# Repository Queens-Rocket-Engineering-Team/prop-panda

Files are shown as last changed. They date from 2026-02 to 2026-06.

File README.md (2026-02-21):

# PANDA Control Board

PANDA (Propulsion Actuation and Nominal Data Acquisition) is the control PCB for the Queen's Rocket Engineering Team's
hybrid rocket engine. During launch, PANDA controls systems on the fill plumbing panel, controls rocket ignition, and
provides pre-launch data acquisition. PANDA also functions as a standalone static fire test stand controller that
can execute all aspects of a hot-fire test.

## Assembled PCB

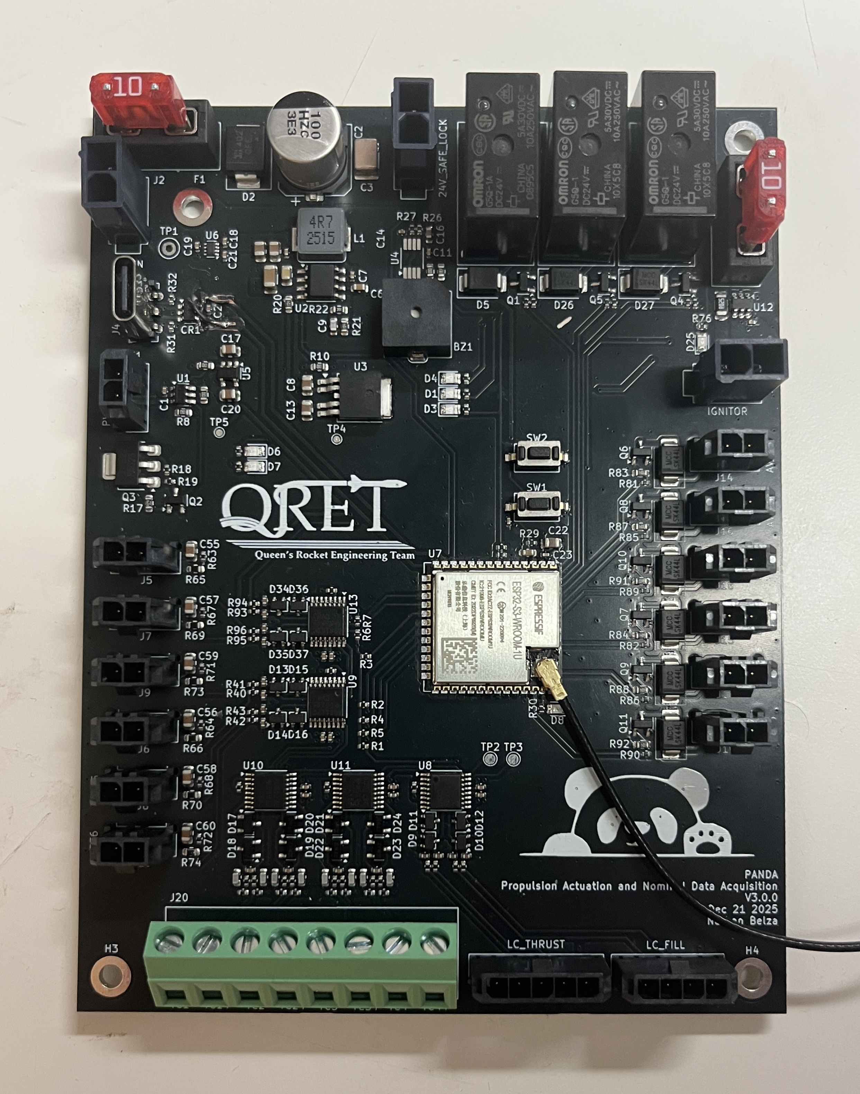
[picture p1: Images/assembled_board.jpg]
Assembled PANDA PCB


## System Architecture

PANDA uses an ESP32S3-WROOM-1U microcontroller for systems control. This ESP32S3 communicates with an external control
server to for remote control and data streaming over 2.4GHz WiFi. All commands are sent from the external server, as
PANDA does not autonomously control any systems.

Five ADS112C04 ADCs provide sensor readings to the ESP32S3 over an I2C bus. Sensors supported are:

- 6 pressure transducers
- 4 thermocouples
- 2 load cells

PANDA is also capable of monitoring ignitor characteristics. Measurements of the current passing through a nichrome wire
ignitor are obtained using a current sense amplifier across a shunt resistor in the ignitor path. Ignitor resistance
readings are also measured by injecting a small current from an IDAC on an ADC, and
measuring the resulting voltage.

A communications diagram for PANDA can be seen below.

```mermaid
---
title: PANDA Communications Flow
---
flowchart LR

    ADC(ADS112C04<br>ADCs) <==I2C==> ESP(ESP32 MCU)

    subgraph Controls
        AV(Actuated Valves)
        24VSAFE[24VSAFE<br>Relay]
        RUN[Ignitor Run<br>Relay]
        PRIME[Ignitor Prime<br>Relay]
    end

    subgraph Sensors
        PT(Pressure Transducers)
        TC(Thermocouples)
        LC(Load Cells)
        CUR(Ignitor Current)
        RES(Ignitor Resistance)
    end

    PT --> ADC
    TC --> ADC
    LC --> ADC
    CUR --> ADC
    RES --> ADC

    ESP --> AV
    ESP -->24VSAFE
    ESP --> RUN
    ESP --> PRIME

    ESP <-. WiFI .-> WIFI(External Server)
```

## Power Architecture

PANDA operates from a 24VDC power supply, and has a maximum current rating of 10A. The 24V rail is first stepped down to 5.3V with a switching converter and then dropped to 5V and 3.3V with LDOs. The 5V rail supplies analog systems, and the 3.3V rail supplies digital systems. Using LDOs on the switching output allows for low-noise power for analog measurements.

The 24VSAFE rail is only be energized when the fill panel is vacated, as it powers hazardous components such as the ignitor. The ignitor utilizes two relays in series for additional redundancy, and to ensure ignition is always intentional. A power distribution chart of PANDA can be seen below. This graph does not include the power sequencing and filtering present on the board.

```mermaid
---
title: PANDA Power Distribution
---
flowchart LR

    24VIN([24VIN]) --> 24VSAFE[24VSAFE<br>Relay]

    subgraph Valves
        AV(Valves)
        AVSAFE(Fill Valve<br>Run Valve)
    end
    24VIN --> AV
    24VSAFE --> AVSAFE

    subgraph Ignitor
        RUN[Ignitor Run<br>Relay]
        RUN --> PRIME[Ignitor Prime<br>Relay]
        PRIME --> IGN(Ignitor)
    end

    24VSAFE --> RUN[Ignitor Run<br>Relay]

    subgraph Voltage Regulation
        BUCK([5.3V Buck])
        BUCK --> 5V([5V LDO])
        BUCK --> 3V3([3.3V LDO])
    end

    24VIN --> BUCK([5.3V Buck])

    subgraph Sensors
        PT(Pressure Transducers)
        LC(Load Cells)
        RES(Ignitor Current<br>Sensor)
    end

    5V --> ADC(ADS112C04<br>ADCs)
    3V3 --> ESP(ESP32 MCU)
    3V3 --> ADC
    24VIN --> PT
    5V --> LC
    5V --> RES
```

## Required Software

This project was created using KiCad v9.0. If manufacturing with JLCPCB, install the Fabrication Toolkit KiCad plugin for JLCPCB.

## Recommended Manufacturing Options

If ordering from JLCPCB, use the JLC04161H-3313 stackup option. For JLC PCBA, the standard PCBA option is required due
to the ESP32S3-WROOM-1U being unavailable as a part in the economic PCBA assembly.

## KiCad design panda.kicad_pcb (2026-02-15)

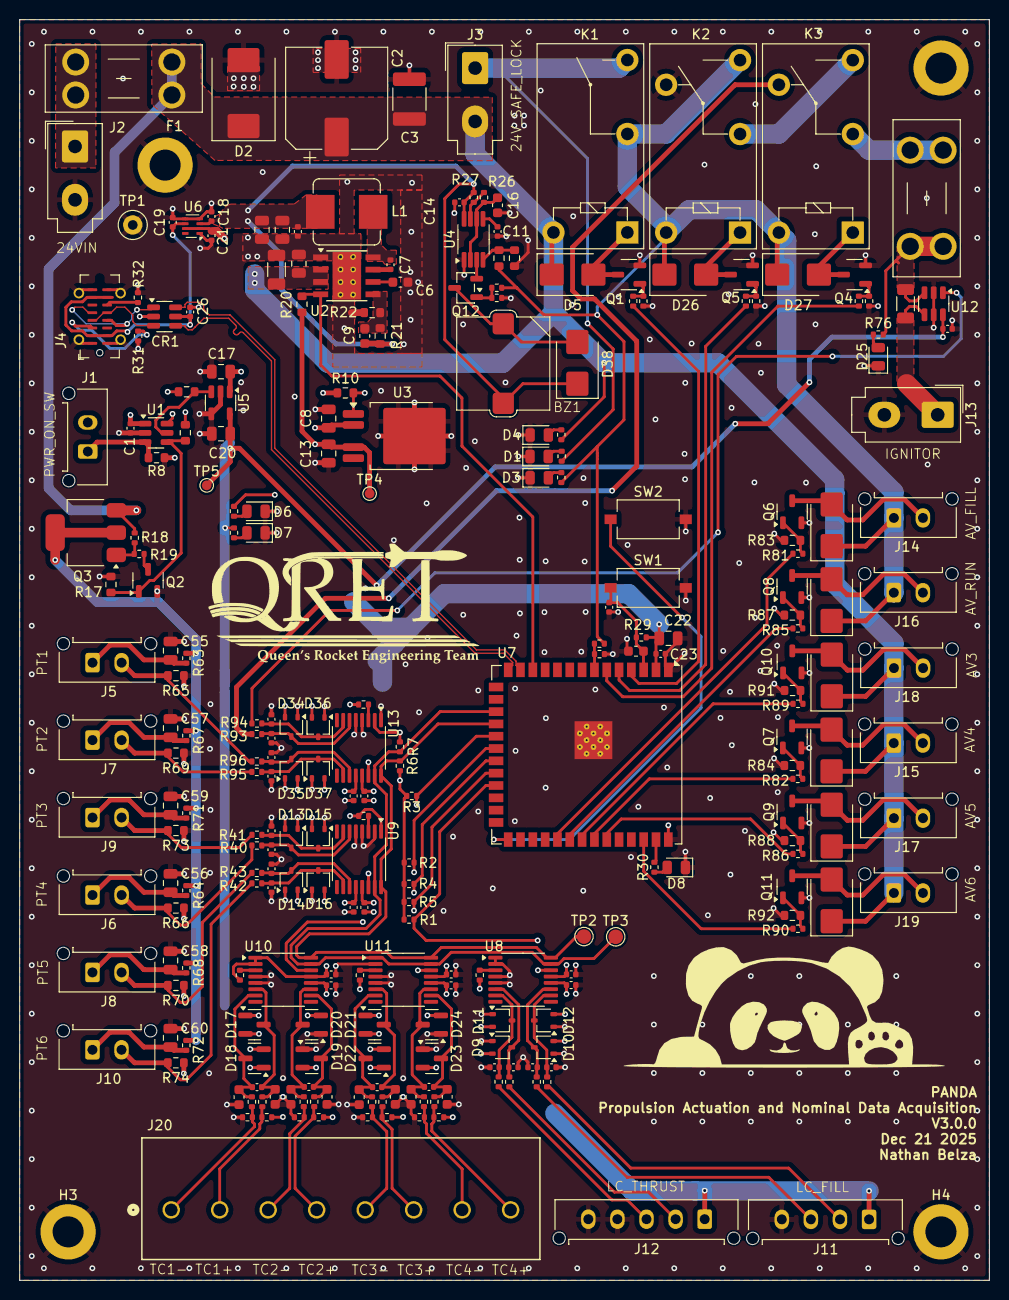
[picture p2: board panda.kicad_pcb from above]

Board: 4 copper layers, 100.0 x 130.0 mm, 268 parts (0 on the bottom side), 135 nets.

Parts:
BZ1: YS-SBZ9650DYB05
C1, C7, C14, C15, C18, C19, C21, C23, C25, C26, C27, C28, C33, C34, C39, C40, C42, C45, C47, C48, C50, C53, C61, C62, C63: 0.1μF; C_0402_1005Metric
C2: 100uF; CP_Elec_10x10
C3: 10uF; C_1812_4532Metric
C4: 10uF; C_1206_3216Metric
C5: 220nF; C_0805_2012Metric
C6, C24: 1uF; C_0603_1608Metric
C8, C13, C17, C20: 10uF; C_0805_2012Metric
C9: 3pF; C_0603_1608Metric
C10, C12, C22: 22uF; C_0805_2012Metric
C11: 10nF; C_0402_1005Metric
C16: 2.2uF; C_0603_1608Metric
C29, C30, C31, C32, C35, C36, C37, C38, C64, C65, C66, C67: 150nF; C_0402_1005Metric
C41, C43, C44, C46, C49, C51, C52, C54: 10nF; C_0603_1608Metric
C55, C56, C57, C58, C59, C60: 3.3uF; C_0805_2012Metric
CR1: USBLC6-2SC6; SOT-23-6
D1, D3, D4, D6, D7, D25: LED-G; LED_0805_2012Metric
D2: SMCJ26A-13-F; D_SMC
D5, D26, D27, D28, D29, D30, D31, D32, D33, D38: SK44BL; D_SMB
D8: LED-Y; LED_0805_2012Metric
D9, D10, D11, D12, D13, D14, D15, D16, D34, D35, D36, D37: BAT54SW; SOT-323_SC-70
D17, D18, D19, D20, D21, D22, D23, D24: BAV199; SOT-23
F1, F2: Fuse; Fuseholder_Blade_Mini_Keystone_3568
H1, H2, H3, H4: MountingHole_Pad; MountingHole_3.2mm_M3_ISO7380_Pad
J1, J5, J6, J7, J8, J9, J10, J14, J15, J16, J17, J18, J19: Conn_01x02; Molex_Micro-Fit_3.0_43650-0215_1x02_P3.00mm_Vertical
J2, J3, J13: Conn_02x01; Molex_Mini-Fit_Jr_5566-02A_2x01_P4.20mm_Vertical
J4: USB_C_Receptacle_USB2.0_16P; USB_C_Receptacle_G-Switch_GT-USB-7051x
J11: 4-Pin Load Cell; Molex_Micro-Fit_3.0_43650-0415_1x04_P3.00mm_Vertical
J12: 5-Pin Load Cell; Molex_Micro-Fit_3.0_43650-0515_1x05_P3.00mm_Vertical
J20: 395934308; CONN_SD-39543-002_NONE_08P_MOL
K1: G5Q-1A DC24; Relay_SPST_Omron-G5Q-1A
K2, K3: G5Q-1 DC24; Relay_SPDT_Omron-G5Q-1
L1: 4.7uH; L_Bourns_SRP7028A_7.3x6.6mm
Q1, Q2, Q4, Q5, Q6, Q7, Q8, Q9, Q10, Q11, Q12: BSS138; SOT-23-3
Q3: DMP6023LE-13; SOT-223-3_TabPin2
R1, R2, R3, R4, R5, R28: 3.3k; R_0402_1005Metric
R6, R7, R30, R35, R36, R37, R38, R40, R41, R42, R43, R49, R50, R51, R52, R58, R59, R60, R61, R94, R95, R96: 1k; R_0402_1005Metric
R8, R10, R12, R14, R20, R21, R23, R83, R84, R87, R88, R91, R92: 100k; R_0603_1608Metric
R9, R11, R13, R34, R76: 39k; R_0402_1005Metric
R15, R18, R19, R27, R29, R39, R44, R53, R62, R77, R78, R97, R98: 10k; R_0402_1005Metric
R16, R79, R80, R81, R82, R85, R86, R89, R90: 100; R_0402_1005Metric
R17: 470k; R_0603_1608Metric
R22: 23.2k; R_0603_1608Metric
R24: 18k; R_0603_1608Metric
R25: 1.2k; R_0402_1005Metric
R26: 160k; R_0402_1005Metric
R31, R32: 5.1k; R_0402_1005Metric
R33: 270k; R_0402_1005Metric
R45, R46, R47, R48, R54, R55, R56, R57: 1M; R_0402_1005Metric
R63, R64, R67, R68, R71, R72: 10; R_0402_1005Metric
R65, R66, R69, R70, R73, R74: 250; R_0603_1608Metric
R75: 10m 1W; R_1206_3216Metric
R93: 47; R_0402_1005Metric
R99: 2.2k; R_0402_1005Metric
SW1, SW2: USAKRO UK-B0227-G4.3-B-250; SW_Tactile_SPST_NO_Straight_CK_PTS636Sx25SMTRLFS
TP1: TestPoint; TestPoint_Loop_D2.50mm_Drill1.0mm
TP2: SDA; TestPoint_Pad_D1.5mm
TP3: SCL; TestPoint_Pad_D1.5mm
TP4: TP_+3.3V; TestPoint_Pad_D1.0mm
TP5: TP_+5V; TestPoint_Pad_D1.0mm
U1: LM3880-1AA; SOT-23-6
U2: LMR33630BDDA; Texas_HSOP-8-1EP_3.9x4.9mm_P1.27mm_ThermalVias
U3: TPS78533QKVURQ1; TO-252-4
U4: TLC555xPS; VSSOP-8_3x3mm_P0.65mm
U5: TPS78450QDBVRQ1; SOT-23-5
U6: LM66200DRLR; SOT-583-8
U7: ESP32-S3-WROOM-1U
U8, U9, U10, U11, U13: ADS112C04; TSSOP-16_4.4x5mm_P0.65mm
U12: INA187A2; SOT-23-6

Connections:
5V_USB: C19.2, C26.1, CR1.5, J4.A4 (VBUS), J4.A9 (VBUS), J4.B4 (VBUS), J4.B9 (VBUS), U6.6 (VIN2)
+3.3V: C13.1, C22.1, C23.1, C27.1, C33.1, C39.1, C47.1, C62.1, R1.1, R2.1, R3.1, R4.1, R5.1, R6.2, R7.2, R20.2, R25.2, R29.2, R39.1, R44.1, R53.1, R62.1, R97.1, TP4.1, U3.4 (OUT), U7.2 (3V3), U8.13 (DVDD), U9.1 (A0), U9.13 (DVDD), U10.1 (A0), U10.2 (A1), U10.13 (DVDD), U11.13 (DVDD), U13.2 (A1), U13.13 (DVDD)
+5V: C20.1, C28.1, C34.1, C40.1, C48.1, C61.2, C63.1, D9.2 (K), D10.2 (K), D11.2 (K), D12.2 (K), D13.2 (K), D14.2 (K), D15.2 (K), D16.2 (K), D17.2 (K), D18.2 (K), D19.2 (K), D20.2 (K), D21.2 (K), D22.2 (K), D23.2 (K), D24.2 (K), D34.2 (K), D35.2 (K), D36.2 (K), D37.2 (K), J11.1, J12.1, R28.2, R45.2, R47.2, R54.2, R56.2, TP5.1, U5.5 (OUT), U8.12 (AVDD), U9.12 (AVDD), U10.12 (AVDD), U11.12 (AVDD), U12.6 (V+), U13.12 (AVDD)
+24V: C2.1, C3.1, C4.1, C5.1, D2.1 (A1), D5.1 (K), D29.1 (K), D31.1 (K), D32.1 (K), D33.1 (K), F1.2, J3.2, J15.1, J17.1, J18.1, J19.1, K1.5, Q3.3 (S), R13.2, R18.2, U2.2 (VIN), U2.3 (EN)
+24V_PT: Q3.2 (D), R63.1, R64.1, R67.1, R68.1, R71.1, R72.1
+24V_SAFE: D26.1 (K), D27.1 (K), D28.1 (K), D30.1 (K), J14.1, J16.1, K1.2, K2.3, K2.5, K3.5, R11.2, R23.2, R33.1, R98.2
/ADC1/AIN0: C30.1, D10.3 (COM), R38.2, U8.11 (AIN0)
/ADC1/AIN1: C32.1, D12.3 (COM), R37.2, U8.10 (AIN1)
/ADC1/AIN2: C31.1, D11.3 (COM), R36.2, U8.7 (AIN2)
/ADC1/AIN3: C29.1, D9.3 (COM), R35.2, U8.6 (AIN3)
/ADC2/AIN0: C36.1, D14.3 (COM), R43.2, U9.11 (AIN0)
/ADC2/AIN1: C38.1, D16.3 (COM), R42.2, U9.10 (AIN1)
/ADC2/AIN2: C37.1, D15.3 (COM), R41.2, U9.7 (AIN2)
/ADC2/AIN3: C35.1, D13.3 (COM), R40.2, U9.6 (AIN3)
/ADC3/AIN0: C53.1, C54.1, D24.3 (common), R61.2, U11.11 (AIN0)
/ADC3/AIN1: C52.2, C53.2, D23.3 (common), R60.2, U11.10 (AIN1)
/ADC3/AIN2: C50.1, C51.1, D22.3 (common), R59.2, U11.7 (AIN2)
/ADC3/AIN3: C49.2, C50.2, D21.3 (common), R58.2, U11.6 (AIN3)
/ADC4/AIN0: C65.1, D35.3 (COM), R96.2, U13.11 (AIN0)
/ADC4/AIN1: C67.1, D37.3 (COM), R95.2, U13.10 (AIN1)
/ADC4/AIN2: C66.1, D36.3 (COM), R94.2, U13.7 (AIN2)
/ADC4/AIN3: C64.1, D34.3 (COM), R93.2, U13.6 (AIN3)
/ADC5/AIN0: C45.1, C46.1, D20.3 (common), R52.2, U10.11 (AIN0)
/ADC5/AIN1: C44.2, C45.2, D19.3 (common), R51.2, U10.10 (AIN1)
/ADC5/AIN2: C42.1, C43.1, D18.3 (common), R50.2, U10.7 (AIN2)
/ADC5/AIN3: C41.2, C42.2, D17.3 (common), R49.2, U10.6 (AIN3)
/ESP32 Breakout/24V_SAFE_DETECT: R33.2, R34.1, U7.7 (IO7)
/ESP32 Breakout/BOOT: SW2.1, U7.27 (IO0)
/ESP32 Breakout/D+: CR1.3, J4.A6 (D+), J4.B6 (D+)
/ESP32 Breakout/D-: CR1.1, J4.A7 (D-), J4.B7 (D-)
/ESP32 Breakout/RESET: C24.1, C25.1, R29.1, SW1.1, U7.3 (EN)
/ESP32 Breakout/USB_N: CR1.6, U7.13 (USB_D-)
/ESP32 Breakout/USB_P: CR1.4, U7.14 (USB_D+)
/ESP32 Breakout/WIFI_IND: R30.2, U7.39 (IO1)
/Ignitor Control/IGNITOR_+VE: J13.1, R75.2, U12.4 (-)
/Ignitor Control/IGN_SUPPLY: F2.2, R75.1, R76.2, U12.3 (+)
/Power Regulation/+3.3V_EN: R10.1, U1.6 (FLAG1), U3.1 (EN)
/Power Regulation/+5.3V: BZ1.1 (+), C9.1, C10.1, C12.1, C14.2, C15.2, C18.2, D38.1 (K), L1.2, R21.1, R27.2, U4.8 (VCC), U6.3 (VIN1)
/Power Regulation/+5V_EN: R12.1, U1.5 (FLAG2), U5.3 (EN)
/Power Regulation/+24V_POST_LCKT: J3.1, K1.3, R9.2
/Power Regulation/PWR_SQ: C1.2, C8.1, C17.1, C21.2, J1.2, R10.2, R12.2, R14.2, U1.1 (VCC), U3.2 (IN), U5.1 (IN), U6.2 (VOUT), U6.7 (VOUT)
/Power Regulation/SW: C7.2, L1.1, U2.8 (SW)
/Power Regulation/TR: C16.1, R26.2, U4.2 (TR), U4.6 (THR)
/Power Regulation/VCC: C6.1, U2.6 (VCC)
BUCK_PG: R20.1, U2.4 (PG), U7.12 (IO8)
DRDY1: R1.2, U7.23 (IO21), U8.14 (DRDY)
DRDY2: R2.2, U7.20 (IO12), U9.14 (DRDY)
DRDY3: R5.2, U7.22 (IO14), U11.14 (DRDY)
DRDY4: R3.2, U7.19 (IO11), U13.14 (DRDY)
DRDY5: R4.2, U7.21 (IO13), U10.14 (DRDY)
GND: C1.1, C2.2, C3.2, C4.2, C5.2, C6.2, C8.2, C10.2, C11.1, C12.2, C13.2, C14.1, C15.1, C16.2, C17.2, C18.1, C19.1, C20.2, C21.1, C22.2, C23.2, C24.2, C25.2, C26.2, C27.2, C28.2, C29.2, C30.2, C31.2, C32.2, C33.2, C34.2, C35.2, C36.2, C37.2, C38.2, C39.2, C40.2, C41.1, C43.2, C44.1, C46.2, C47.2, C48.2, C49.1, C51.2, C52.1, C54.2, C55.2, C56.2, C57.2, C58.2, C59.2, C60.2, C61.1, C62.2, C63.2, C64.2, C65.2, C66.2, C67.2, CR1.2, D1.1 (K), D2.2 (A2), D3.1 (K), D4.1 (K), D6.1 (K), D7.1 (K), D8.1 (K), D9.1 (A), D10.1 (A), D11.1 (A), D12.1 (A), D13.1 (A), D14.1 (A), D15.1 (A), D16.1 (A), D17.1 (A), D18.1 (A), D19.1 (A), D20.1 (A), D21.1 (A), D22.1 (A), D23.1 (A), D24.1 (A), D25.1 (K), D34.1 (A), D35.1 (A), D36.1 (A), D37.1 (A), H1.1, H2.1, H3.1, H4.1, J2.2, J4.A1 (GND), J4.A12 (GND), J4.B1 (GND), J4.B12 (GND), J4.S1 (SHIELD), J11.4, J12.4, J12.5, J13.2, K2.4, Q1.2 (S), Q2.2 (S), Q4.2 (S), Q5.2 (S), Q6.2 (S), Q7.2 (S), Q8.2 (S), Q9.2 (S), Q10.2 (S), Q11.2 (S), R8.1, R15.2, R17.1, R22.2, R24.1, R31.2, R32.2, R34.2, R46.1, R48.1, R55.1, R57.1, R65.2, R66.2, R69.2, R70.2, R73.2, R74.2, R77.2, R78.2, R83.2, R84.2, R87.2, R88.2, R91.2, R92.2, R99.1, SW1.2, SW2.2, TP1.1, U1.2 (GND), U2.1 (GND), U2.9 (GND), U3.3 (GND), U4.1 (GND), U5.2 (GND), U5.4 (GND), U6.1 (GND), U6.4 (~ON), U6.5 (GND), U7.1 (GND), U7.40 (GND), U7.41 (GND), U8.1 (A0), U8.2 (A1), U8.4 (DGND), U8.5 (AVSS), U9.2 (A1), U9.4 (DGND), U9.5 (AVSS), U10.4 (DGND), U10.5 (AVSS), U11.2 (A1), U11.4 (DGND), U11.5 (AVSS), U12.2 (GND), U12.5 (REF), U13.1 (A0), U13.4 (DGND), U13.5 (AVSS)
I2C_SCL: R6.1, TP2.1, U7.18 (IO10), U8.16 (SCL), U9.16 (SCL), U10.16 (SCL), U11.16 (SCL), U13.16 (SCL)
I2C_SDA: R7.1, TP3.1, U7.17 (IO9), U8.15 (SDA), U9.15 (SDA), U10.15 (SDA), U11.1 (A0), U11.15 (SDA), U13.15 (SDA)
IGNITOR_PRIME_CTL: R79.2, U7.6 (IO6)
IGNITOR_RUN_CTL: R80.2, U7.5 (IO5)
IGN_CURRENT_READ: R94.1, U12.1
IGN_RESIST_READ: K3.4, R93.1
LC_FILL_+: J11.2, R37.1
LC_FILL_-: J11.3, R38.1
LC_THRUST_+: J12.2, R35.1
LC_THRUST_-: J12.3, R36.1
unnamed: BZ1.2 (-), D38.2 (A), Q12.3 (D)
unnamed: D1.2 (A), R9.1
unnamed: D3.2 (A), R11.1
unnamed: D4.2 (A), R13.1
unnamed: D5.2 (A), K1.1, Q1.3 (D)
unnamed: D6.2 (A), R25.1
unnamed: D7.2 (A), R28.1
unnamed: D8.2 (A), R30.1
unnamed: D25.2 (A), R76.1
unnamed: D26.2 (A), K2.1, Q5.3 (D)
unnamed: D27.2 (A), K3.1, Q4.3 (D)
unnamed: D28.2 (A), J14.2, Q6.3 (D)
unnamed: D29.2 (A), J15.2, Q7.3 (D)
unnamed: D30.2 (A), J16.2, Q8.3 (D)
unnamed: D31.2 (A), J17.2, Q9.3 (D)
unnamed: D32.2 (A), J18.2, Q10.3 (D)
unnamed: D33.2 (A), J19.2, Q11.3 (D)
unnamed: F2.1, K3.2
unnamed: J1.1, R8.2, U1.3 (EN)
unnamed: F1.1, J2.1
unnamed: J4.A5 (CC1), R31.1
unnamed: J4.B5 (CC2), R32.1
unnamed: C55.1, J5.1, R63.2
unnamed: C56.1, J6.1, R64.2
unnamed: C57.1, J7.1, R67.2
unnamed: C58.1, J8.1, R68.2
unnamed: C59.1, J9.1, R71.2
unnamed: C60.1, J10.1, R72.2
unnamed: K2.2, K3.3
unnamed: Q1.1 (G), R15.1, R16.1
unnamed: Q2.3 (D), R19.1
unnamed: Q2.1 (G), R14.1, R17.2, U1.4 (FLAG3)
unnamed: Q3.1 (G), R18.1, R19.2
unnamed: Q4.1 (G), R77.1, R79.1
unnamed: Q5.1 (G), R78.1, R80.1
unnamed: Q6.1 (G), R81.2, R83.1
unnamed: Q7.1 (G), R82.2, R84.1
unnamed: Q8.1 (G), R85.2, R87.1
unnamed: Q9.1 (G), R86.2, R88.1
unnamed: Q10.1 (G), R89.2, R91.1
unnamed: Q11.1 (G), R90.2, R92.1
unnamed: Q12.1 (G), R98.1, R99.2
unnamed: Q12.2 (S), U4.3 (Q)
unnamed: C7.1, U2.7 (BOOT)
unnamed: C9.2, R21.2, R22.1, U2.5 (FB)
unnamed: C11.2, U4.5 (CV)
unnamed: R26.1, R27.1, U4.7 (DIS)
unnamed: R23.1, R24.2, U4.4 (R)
unnamed: R39.2, U8.3 (RESET)
unnamed: R44.2, U9.3 (RESET)
unnamed: R53.2, U10.3 (RESET)
unnamed: R62.2, U11.3 (RESET)
unnamed: R97.2, U13.3 (RESET)
PT_READ_1: J5.2, R65.1, R96.1
PT_READ_2: J7.2, R69.1, R95.1
PT_READ_3: J9.2, R41.1, R73.1
PT_READ_4: J6.2, R40.1, R66.1
PT_READ_5: J8.2, R43.1, R70.1
PT_READ_6: J10.2, R42.1, R74.1
SAFE_24V_CTL: R16.2, U7.4 (IO4)
TC1+: J20.2, R45.1, R49.1
TC1-: J20.1, R46.2, R50.1
TC2+: J20.4, R47.1, R51.1
TC2-: J20.3, R48.2, R52.1
TC3+: J20.6, R54.1, R58.1
TC3-: J20.5, R55.2, R59.1
TC4+: J20.8, R56.1, R60.1
TC4-: J20.7, R57.2, R61.1
VALVE_1_CTL: R81.1, U7.31 (IO38)
VALVE_2_CTL: R85.1, U7.32 (IO39)
VALVE_3_CTL: R89.1, U7.33 (IO40)
VALVE_4_CTL: R82.1, U7.34 (IO41)
VALVE_5_CTL: R86.1, U7.35 (IO42)
VALVE_6_CTL: R90.1, U7.38 (IO2)

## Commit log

2025-11-06 Update date
    [panda.kicad_pcb]
2025-11-07 minor fixed + lowered status leds to ~0.6mA, which should give ~50 mcd
    [ESP32Breakout.kicad_sch, Ignitor_Control.kicad_sch, PowerRegulation.kicad_sch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]
2025-11-07 updated name on pcb
    [panda.kicad_pcb]
2025-11-09 revamped schematic to be more readable
    [ADCCircuitry.kicad_sch, ESP32Breakout.kicad_sch, Ignitor_Control.kicad_sch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]
2025-11-09 remove diode between 5V and 5V_USB due to oversight (ADS112C04 cannot have DVDD without AVDD)
    [ESP32Breakout.kicad_sch, PowerRegulation.kicad_sch, panda.kicad_sch]
2025-11-11 add power sequencing
    add usb VBUS ORing
    [ESP32Breakout.kicad_sch, Ignitor_Control.kicad_sch, PowerRegulation.kicad_sch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]
2025-11-11 add thermocouple filtering, add 5th ADC
    [ADCCircuitry.kicad_sch, PowerRegulation.kicad_sch, ThermocoupleADC.kicad_sch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]
2025-11-11 grounded usb-c receptacle shield
    [ESP32Breakout.kicad_sch, PowerRegulation.kicad_sch, ThermocoupleADC.kicad_sch]
2025-11-16 minor fixes
    [ESP32Breakout.kicad_sch, Ignitor_Control.kicad_sch, PowerRegulation.kicad_sch]
2025-11-17 add 2 stage lockout to ignitor, add ignitor resistance reading with adc current source
    [ADCCircuitry.kicad_sch, ESP32Breakout.kicad_sch, Ignitor_Control.kicad_sch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]
2025-11-17 fix ignitor resistance read circuit to use correct PGA reference
    [IgnitorADC.kicad_sch, Ignitor_Control.kicad_sch, panda.kicad_sch]
2025-11-17 add periodic buzzer alert to +24V_SAFE
    [PowerRegulation.kicad_sch]
2025-11-17 ground floating trace between ign relays when relays open
    [ESP32Breakout.kicad_sch, Ignitor_Control.kicad_sch, PowerRegulation.kicad_sch]
2025-11-21 add rc filters to pressure transducer power in to filter 500khz signal on 24v rail
    [Ignitor_Control.kicad_sch, PowerRegulation.kicad_sch, PressureTransducerMeasurement.kicad_sch]
2025-11-21 add some comments to clarify ign_resist_read circuitry and implementation
    [IgnitorADC.kicad_sch, Ignitor_Control.kicad_sch, panda.kicad_sch]
2025-11-22 change buck converter to hopefully remove some noise on 24v
    [PowerRegulation.kicad_sch]
2025-11-25 add capacitor and resistor footprints
    [ADCCircuitry.kicad_sch, ESP32Breakout.kicad_sch, IgnitorADC.kicad_sch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]
2025-11-27 start pcb design
    [PowerRegulation.kicad_sch, panda.kicad_pcb]
2025-12-01 change connectors and more progress on pcb
    [ESP32Breakout.kicad_sch, IgnitorADC.kicad_sch, Ignitor_Control.kicad_sch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]
2025-12-06 change clamping resistors on tc adcs for lower leakage current
    [ADCCircuitry.kicad_sch, ESP32Breakout.kicad_sch, IgnitorADC.kicad_sch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]
2025-12-21 Add identifying silkscreen text and icons
    [panda.kicad_pcb]
2025-12-21 Fix all silkscreen overlaps and violations
    [panda.kicad_pcb]
2025-12-21 Resolve DRC issues
    [panda.kicad_pcb]
2025-12-22 fix buzzer footprint to remove silkscreen pad overlap
2025-12-22 add silkscreen labels to connectors, remove pick Rb message (was already chosen)
    [ThermocoupleADC.kicad_sch, panda.kicad_pcb]
2025-12-30 Update version number in KiCad files
    [ADCCircuitry.kicad_sch, ESP32Breakout.kicad_sch, IgnitorADC.kicad_sch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]
2025-12-31 Update with new production files. Change CSA to INA187A2 (from A1 skew) for LCSC availability reasons.
    [Ignitor_Control.kicad_sch]
2026-01-21 fix inverted usb lines
    [ESP32Breakout.kicad_sch]
2026-01-21 fix usb data traces on pcb
    [panda.kicad_pcb]
2026-01-29 add nmos to buzzer to keep off when 24vSAFE off
    [PowerRegulation.kicad_sch, panda.kicad_pcb]
2026-02-05 fix adc numbering
    [panda.kicad_sch]
2026-02-07 fix usb traces to be 90 ohms impedance
    [panda.kicad_pcb]
2026-02-14 fix adc numbering on schematic
    [panda.kicad_sch]
2026-02-15 fix drdy pin numbering
    [ESP32Breakout.kicad_sch, panda.kicad_pcb, panda.kicad_sch]
2026-02-17 update readme board picture
2026-06-25 update board image again
